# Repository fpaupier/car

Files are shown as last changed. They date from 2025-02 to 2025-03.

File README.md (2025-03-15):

# ESP-NOW Controlled RC Car





This project documents how to build a simple remote-controlled car using an ESP32 microcontroller and the ESP-NOW
protocol for wireless communication.

<div align="center">
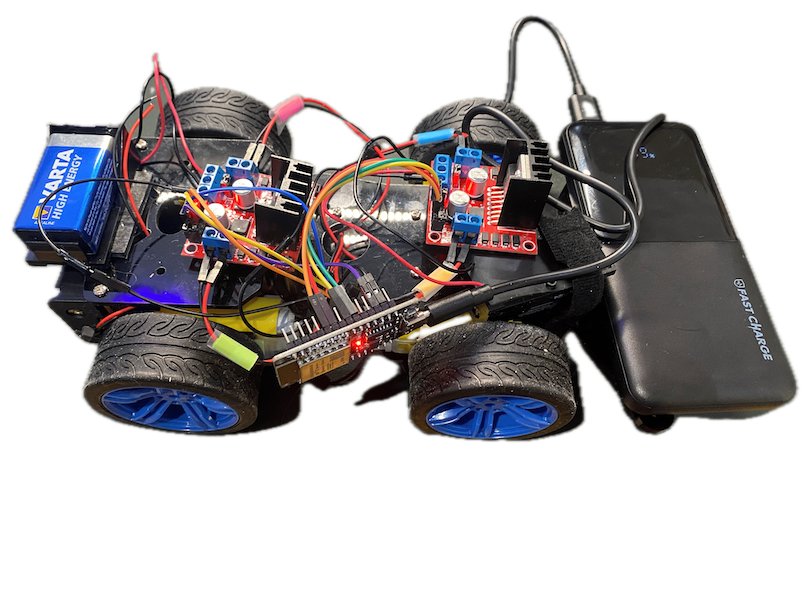
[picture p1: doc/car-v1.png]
car
  
</div>

> We achieved a control range of up to 115 meters between the receiver (car) and transmitter (controller).

For the controller-related parts and code, refer to the dedicated
repository: [github.com/fpaupier/car-transmitter](https://github.com/fpaupier/car-transmitter)

## Hardware - Building the car

The car uses a standard 4-wheel chassis with DC motors controlled by H-bridge motor drivers. An ESP32 serves as the
brain of the operation, receiving commands via ESP-NOW protocol from a joystick controller.

### Sourcing the components

## Bill of material - Components and their sources (prices as of March 2025)

| Component | Image | Source | Price (EUR) | Quantity | Total Price (EUR) |
|---|---|---|---|---|---|
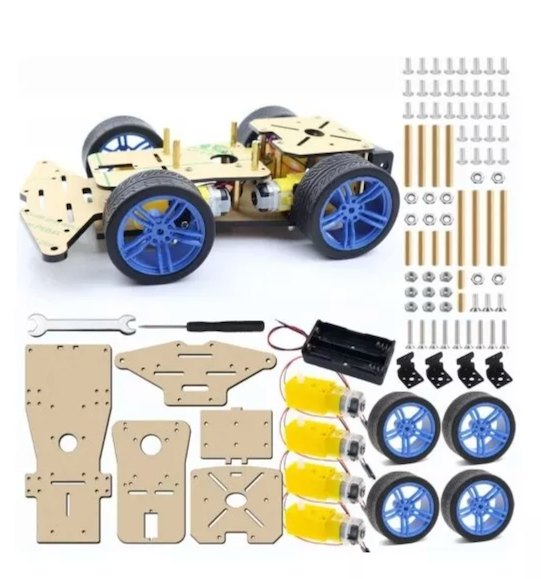
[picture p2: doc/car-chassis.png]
chassis
| 4-wheel car chassis |  | [Kubii](https://www.kubii.com/en/robots-extensions/3773-car-chassis-robot-kit-for-raspberry-pi-and-arduino-3272496312517.html) | 36.96 | 1 | 36.96 |
| DC Motors (3-12V) | *Included with chassis* | Included with chassis | - | 4 | - |
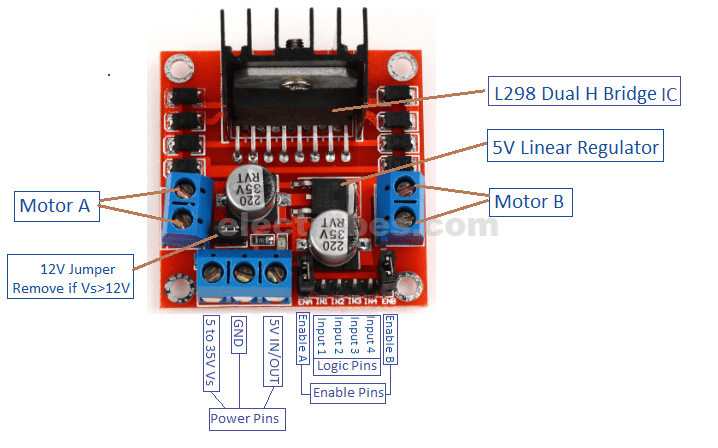
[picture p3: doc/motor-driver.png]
L298N
| H-bridge L298N |   | [Amazon.fr](https://amzn.eu/d/dbmBLjt) | 5.34 | 2 | 10.69 |
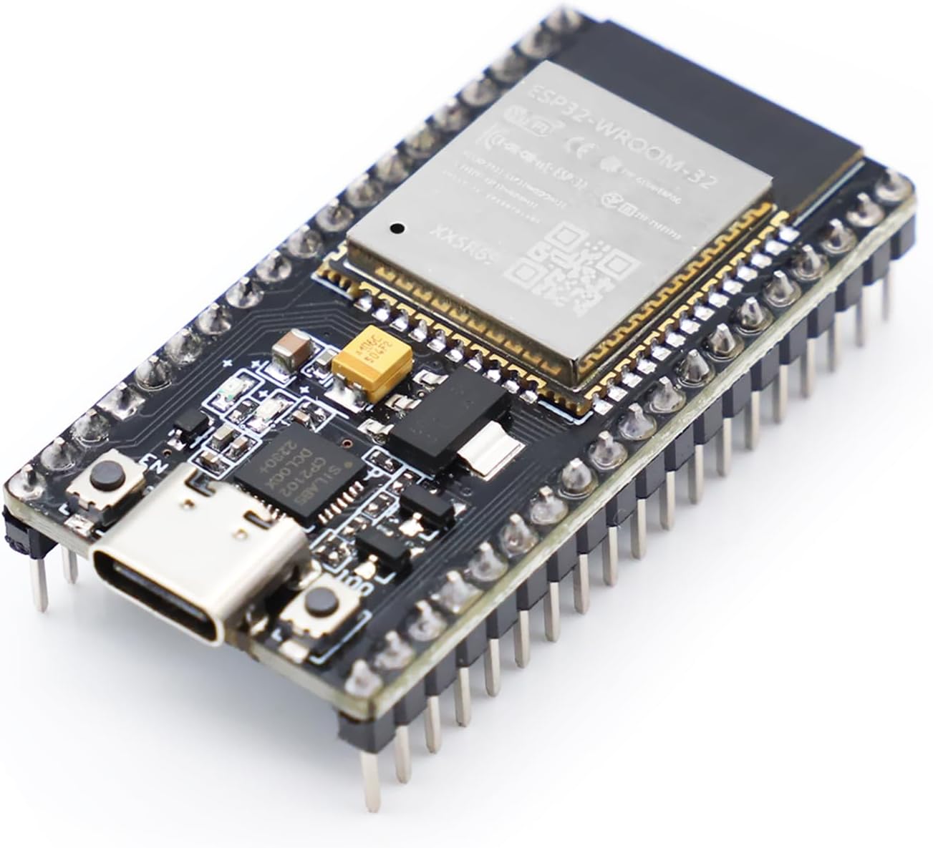
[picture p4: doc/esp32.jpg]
ESP32
| ESP32 WROOM-32 |  | [Amazon.fr](https://amzn.eu/d/a1N37u4) | 8.99 | 1 | 8.99 |
| Powerbank (to power the ESP32) | | Generic | 15.00 | 1 | 15.00 |
| 9V Batteries (to power the motors) | | [Amazon.fr](https://amzn.eu/d/emOUOg1) | 3.50 | 2 | 8.99 |
| Battery connectors | | [Amazon.fr](https://amzn.eu/d/2nVmRUF) | 5.00 | 2 | 9.99 |
| **Total** | | | | | **90.62€** |

### Wiring Instructions

#### Motor Driver Connections

##### Front Motors (L298N 2)

| ESP32 Pin | L298N Pin | Description |
|---|---|---|
| GPIO 16 | IN1 | Front left motor forward |
| GPIO 17 | IN2 | Front left motor backward |
| GPIO 18 | IN3 | Front right motor forward |
| GPIO 19 | IN4 | Front right motor backward |
| GPIO 27 | ENA | Front left motor PWM speed control  |
| GPIO 26 | ENB | Front right motor PWM speed control |
| 5V | 5V | Logic power supply |
| GND | GND | Ground connection |

##### Rear Motors (L298N 1)

| ESP32 Pin | L298N Pin | Description |
|---|---|---|
| GPIO 12 | IN1 | Rear left motor forward |
| GPIO 13 | IN2 | Rear left motor backward |
| GPIO 14 | IN3 | Rear right motor forward |
| GPIO 15 | IN4 | Rear right motor backward |
| GPIO 25 | ENA | Rear left motor PWM speed control  |
| GPIO 32 | ENB | Rear right motor PWM speed control |
| 5V | 5V | Logic power supply |
| GND | GND | Ground connection |

#### PWM Configuration

The code uses 4 PWM channels for speed control, this enables to use the analog joystick value for progressive speed.

- Channel 0: Front left motor
- Channel 1: Front right motor
- Channel 2: Rear left motor
- Channel 3: Rear right motor

PWM is configured with a frequency of 5000Hz and 8-bit resolution (0-255 values).

#### Power Connections

- ESP32: Powered via USB from the powerbank
- Motors: Powered by two 9V batteries connected to the L298N's power inputs
- Built-in LED: GPIO 2 is used for status indication

#### Power Connections

- ESP32: Powered via USB from the powerbank
- Motors: Powered by two 9V batteries connected to the L298N's power input

## Software - Code to Run the Car

> **Prerequisite**: This project uses PlatformIO to build and upload code to the ESP32. You will need to install it -
> see [PlatformIO.org](https://platformio.org/)

### Getting Your ESP32's MAC Address

Since we use [ESP-NOW](https://docs.espressif.com/projects/esp-idf/en/stable/esp32/api-reference/network/esp_now.html)
for communication, you'll need to know your car's MAC address to configure the controller. Run this code on your car's
ESP32:

```cpp

#include

void setup() {
Serial.begin(115200);
WiFi.mode(WIFI_STA); // Set as WiFi station
delay(100); // Short delay for initialization
}

void loop() {
Serial.print("ESP32 Car MAC Address: ");
Serial.println(WiFi.macAddress());
}

```

### Source Code Structure

```

car/
├── src/
│ └── main.cpp // Main program flow

```

### Getting Started

1. Clone the repository
2. Build the project using PlatformIO
3. Upload to your ESP32 and monitor the serial output
4. Use the joystick controller to pilot the car

## Troubleshooting

- If motors don't respond, check battery levels and connections
- Ensure both the car and controller are powered on
- For optimal range, keep the ESP builtin antennas unobstructed

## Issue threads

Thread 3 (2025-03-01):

Fix alimentation to use proper battery for the whole setup

fpaupier, 2025-03-01:
- remove the powerbank which is very heavy in the front of the car
- make sure to share ground

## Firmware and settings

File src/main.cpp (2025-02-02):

#include <esp_now.h>
#include <WiFi.h>
#include <Arduino.h>
#include <driver/ledc.h>


// Rear Motors (L298N 1)
#define REAR_LEFT_IN1  12
#define REAR_LEFT_IN2  13
#define REAR_RIGHT_IN3 14
#define REAR_RIGHT_IN4 15

// Front Motors (L298N 2)
#define FRONT_LEFT_IN1 16
#define FRONT_LEFT_IN2 17
#define FRONT_RIGHT_IN3 18
#define FRONT_RIGHT_IN4 19

#define TIMEOUT_MS      2000

// PWM Configuration
#define PWM_FREQ        5000
#define PWM_RESOLUTION  8

// Add enable pin definitions
#define ENA_FRONT 27
#define ENB_FRONT 26
#define ENA_REAR  25
#define ENB_REAR  32

#define PWM_CHANNEL_FL  0
#define PWM_CHANNEL_FR  1
#define PWM_CHANNEL_RL  2
#define PWM_CHANNEL_RR  3

#ifndef LED_BUILTIN
#define LED_BUILTIN 2
#endif


// Data structure for joystick values
typedef struct struct_message {
    int x;
    int y;
    bool button;
} struct_message;

unsigned long lastReceiveTime = 0;


// Motor control functions

void setMotor(int channel, int pinA, int pinB, int speed) {
    bool forward = speed >= 0;
    int absSpeed = abs(speed);

    digitalWrite(pinA, forward ? HIGH : LOW);
    digitalWrite(pinB, forward ? LOW : HIGH);
    ledcWrite(channel, absSpeed);
}

void controlMotors(int left, int right) {
    Serial.printf("Control motors left: %4d | Right: %4d\n", left, right);
    setMotor(PWM_CHANNEL_RL, REAR_LEFT_IN1, REAR_LEFT_IN2, left);
    setMotor(PWM_CHANNEL_FL, FRONT_LEFT_IN1, FRONT_LEFT_IN2, left);
    setMotor(PWM_CHANNEL_RR, REAR_RIGHT_IN3, REAR_RIGHT_IN4, right);
    setMotor(PWM_CHANNEL_FR, FRONT_RIGHT_IN3, FRONT_RIGHT_IN4, right);
}


void stopAllMotors() {
    ledcWrite(PWM_CHANNEL_RL, 0);
    ledcWrite(PWM_CHANNEL_RR, 0);
    ledcWrite(PWM_CHANNEL_FL, 0);
    ledcWrite(PWM_CHANNEL_FR, 0);
}

void setupMotors() {
    pinMode(ENA_FRONT, OUTPUT);
    pinMode(ENB_FRONT, OUTPUT);
    pinMode(ENA_REAR, OUTPUT);
    pinMode(ENB_REAR, OUTPUT);
    pinMode(REAR_LEFT_IN1, OUTPUT);
    pinMode(REAR_LEFT_IN2, OUTPUT);
    pinMode(REAR_RIGHT_IN3, OUTPUT);
    pinMode(REAR_RIGHT_IN4, OUTPUT);
    pinMode(FRONT_LEFT_IN1, OUTPUT);
    pinMode(FRONT_LEFT_IN2, OUTPUT);
    pinMode(FRONT_RIGHT_IN3, OUTPUT);
    pinMode(FRONT_RIGHT_IN4, OUTPUT);
}

void setupPWM() {
    // Setup PWM channels
    ledcSetup(PWM_CHANNEL_FL, PWM_FREQ, PWM_RESOLUTION);
    ledcSetup(PWM_CHANNEL_FR, PWM_FREQ, PWM_RESOLUTION);
    ledcSetup(PWM_CHANNEL_RL, PWM_FREQ, PWM_RESOLUTION);
    ledcSetup(PWM_CHANNEL_RR, PWM_FREQ, PWM_RESOLUTION);

    // Attach PWM to enable pins
    ledcAttachPin(ENA_FRONT, PWM_CHANNEL_FL);
    ledcAttachPin(ENB_FRONT, PWM_CHANNEL_FR);
    ledcAttachPin(ENA_REAR, PWM_CHANNEL_RL);
    ledcAttachPin(ENB_REAR, PWM_CHANNEL_RR);
}

// ESP-NOW callback
void OnDataRecv(const uint8_t *mac, const uint8_t *incomingData, int len) {
    struct_message joystickData;
    memcpy(&joystickData, incomingData, sizeof(joystickData));
    Serial.printf("X: %4d | Y: %4d | BTN: %d\n", joystickData.x, joystickData.y, joystickData.button);
    lastReceiveTime = millis();

    // Calculate motor speeds
    int leftSpeed = constrain(joystickData.y + joystickData.x, -255, 255);
    int rightSpeed = constrain(joystickData.y - joystickData.x, -255, 255);

    controlMotors(leftSpeed, rightSpeed);
}


void setup() {
    Serial.begin(115200);
    pinMode(LED_BUILTIN, OUTPUT);

    setupMotors();
    setupPWM();

    // Init ESP-NOW
    WiFi.mode(WIFI_STA);
    if (esp_now_init() != ESP_OK) {
        Serial.println("Error initializing ESP-NOW");
        return;
    }
    Serial.println("ESP-NOW initialized");

    esp_now_register_recv_cb(OnDataRecv);
}

void loop() {
    unsigned long currentTime = millis();
    if (currentTime - lastReceiveTime > TIMEOUT_MS) {
        stopAllMotors();
        digitalWrite(LED_BUILTIN, !digitalRead(LED_BUILTIN));
        delay(100);
    } else {
        digitalWrite(LED_BUILTIN, HIGH);
    }
}

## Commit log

2025-01-26 add(sample blink led)
2025-02-02 update(PWM control) wip
2025-03-16 add(CAD): files
    #4
    [ESP-NOW-RC-Car.kicad_pcb, ESP-NOW-RC-Car.kicad_sch]
2025-03-17 update(CAD): files
    WIP
    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
    [ESP-NOW-RC-Car.kicad_sch]
